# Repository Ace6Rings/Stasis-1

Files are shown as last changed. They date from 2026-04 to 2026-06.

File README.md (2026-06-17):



# OVERVIEW

The Reshular Robot Arm is a 6 DOF robotic arm. It is operated over bluetooth so it can be operated remotely.
5 stepper motors, using the TMC2209 driver, and 1 servo motor is used to make this huge robotic arm.

# Purpose

I made this because I've always been fascinated on how to use technology to make an impact on the physical world. 
I've seen small robotic arms powered with servo motors. But I noticed that scaling it up in size changes the materials I need 
and introduces (newish) problems like insufficient torque when using a servo motor. These robotic arms are also shorter ranged and can only hold
very light and small items. Thats why I built this robotic arm. I can lift items that are impossible for small robotic arms like a big book. 
The most important thing is that I became way better at eda since this is my first project that uses a smd PCB.

# Schematic
schematic 2
scematic1
There are 5 tmc 2209 motor drivers. They are almost identical. Only their gpio assignments to dir and step changes and also their uart configuration.

So how did I configure it and how can you too?

The tmc2209 talks to the esp32 via UART. But four tmc 2209s share one uart line. Wait, there's 5 tmcs, not 4! How could that be?
Well, the ID for uart is dictated by the whether your ms1 and ms2 are pulled high or low. Since there are 2 states and 2 pins, 2^2 is 4. So you get 4 combinations.
To account for the 5th tmc 2209, I just used another set of gpios.

The ms1 and ms2 pins also happen to control microstepping, and thats pretty important if you have something like an EV or a robot arm like this. So I put the finer microstepping onto parts that actually matter, such as the elbow joint. You can find further details via the datasheet for the TMC2209 and the exact configuration in the PCB file that I have.
# PCB
pcb

Now lets get into the PCB.
The specs of the PCB isn't anything special. It is a 2 layer pcb, and thats exactly why this is good. It's theoretically not gonna perform as well as a four layer board (well not really because this is a 2 layer board thing). But since its only 2 layers, the cost decreases significantly. There are two layers of electrical protection. The first one is the NCP1117 (well not really? but if it dies the circuit becomes open so I guess it is protection), and the second one is the TVS diode. The TVS diode is a component that protects your circuit when the voltage/current reaches a certain threshold. For something like a robot arm, you will defininately one that.
# Model
The purpose of the model is not to make it look good but to make it as light as possible to test in real life. 
It features 6 degrees of freedom, which could move (almost) ny item in any way you could think of.
model2
model1
The base has an hexagonal pattern which maximizes strength, aesthetics, and filament efficiency.
# Motor joints

Well, how does each joint work? Its actually quite simple. You can tell by the picture that the stepper motors are directly attached to each joint, so no special pullys or anything! This saves complexity and cost. For the gripper, its a little different.

The central gear meshes with the two side parts. When it spins, the two grippers come together and, well, grips. Spinning it the opposite way retracts it. You can try it out in this link.
https://cad.onshape.com/documents/dfb7d85a38278a669fcebbb5/w/2d92252d034fc83197e6695c/e/ec9dc79179103d4b89a939a4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



As you can see, the motor is directly attached.

# Testing

N/A (will include after getting parts)

# Bill of Materials

| Name | Purpose | Quantity | Total Cost (USD) | Link | Distributor |
|---|---|---|---|---|---|
| li ion batteries | batteries to power my robot arm | 1 | 25.98 | https://www.amazon.com/Mupoer-Rechargeable-Batteries-Integrated-Charging/dp/B0D4M581B3/ref=sr_1_15?sr=8-15 | amazon |
| ds3225 | gripper motor | 1 | 16.99 | https://www.amazon.com/gp/product/B0CNTG877G/ref=ox_sc_act_title_1?smid=A1PKC2PUMNR8VD | amazon |
| HEAT SET INSERTS | To assemble my robot arm | 1 | 9.98 | https://www.amazon.com/M2-M2-5-M3-Threaded-Inserts/dp/B0FH4JQ3VB/ref=sr_1_4?sr=8-4 | amazon |
| 175-TMC2209-LA-TCT-ND | IC MTR DRV 4.75-28V QFN28 | 10 | 40.89 | https://www.digikey.com/en/products/detail/analog-devices-inc-maxim-integrated/TMC2209-LA-T/10232491 | DIGIKEY |
| NCP1117LPST33T3GOSCT-ND | IC REG LINEAR 3.3V 1A SOT-223 | 10 | 2.62 | https://www.digikey.com/en/products/detail/onsemi/NCP1117LPST33T3G/1967376 | DIGIKEY |
| 296-50511-1-ND | UNIDIR PRECISION SURGE DIODE | 10 | 7.06 | https://www.digikey.com/en/products/detail/texas-instruments/TVS1400DRVR/11589096 | DIGIKEY |
| 2073-USB4085-GF-ACT-ND | CONN RCPT USB2.0 TYPE C 16+8POS | 2 | 2.15 | https://www.digikey.com/en/products/detail/gct/USB4085-GF-A/9859704 | DIGIKEY |
| CKN10285CT-ND | SWITCH TACTILE SPST-NO 0.05A 32V | 10 | 5.81 | https://www.digikey.com/en/products/detail/c-k/KMR241NG-ULC-LFS/2747141 | DIGIKEY |
| 490-10700-1-ND | CAP CER 0.1UF 50V X7R 0402 | 50 | 0.81 | https://www.digikey.com/en/products/detail/murata-electronics/GRM155R71H104KE14D/4358653 | DIGIKEY |
| 277-1722-ND | TERM BLK 3POS SIDE ENT 3.5MM PCB | 1 | 2.10 | https://www.digikey.com/en/products/detail/phoenix-contact/1984620/950937 | DIGIKEY |
| 1276-1096-1-ND | CAP CER 10UF 16V X5R 0805 | 10 | 0.54 | https://www.digikey.com/en/products/detail/samsung-electro-mechanics/CL21A106KOQNNNE/3886902 | DIGIKEY |
| 273-KDV12DR100ETCT-ND | RES 0.1 OHM 0.5% 1/2W 1206 | 25 | 3.00 | https://www.digikey.com/en/products/detail/ohmite/KDV12DR100ET/13691867 | DIGIKEY |
| 311-5.10KLRCT-ND | RES 5.1K OHM 1% 1/16W 0402 | 25 | 0.37 | https://www.digikey.com/en/products/detail/yageo/RC0402FR-075K1L/726633 | DIGIKEY |
| 541-10.0KLCT-ND | RES 10K OHM 1% 1/16W 0402 | 25 | 0.59 | https://www.digikey.com/en/products/detail/vishay-dale/CRCW040210K0FKED/1176095 | DIGIKEY |
| 311-100KLRCT-ND | RES 100K OHM 1% 1/16W 0402 | 25 | 0.37 | https://www.digikey.com/en/products/detail/yageo/RC0402FR-07100KL/726651 | DIGIKEY |
| 311-1.00KLRCT-ND | RES 1K OHM 1% 1/16W 0402 | 25 | 0.37 | https://www.digikey.com/en/products/detail/yageo/RC0402FR-071KL/726544 | DIGIKEY |
| 277-1721-ND | TERM BLK 2POS SIDE ENT 3.5MM PCB | 1 | 1.46 | https://www.digikey.com/en/products/detail/phoenix-contact/1984617/950934 | DIGIKEY |
| 490-4763-1-ND | CAP CER 0.022UF 50V X7R 0402 | 50 | 1.01 | https://www.digikey.com/en/products/detail/murata-electronics/GCM155R71H223KA55D/2756835 | DIGIKEY |
| 277-1860-ND | TERM BLK 4POS SIDE ENT 3.5MM PCB | 5 | 13.45 | https://www.digikey.com/en/products/detail/phoenix-contact/1984633/950950 | DIGIKEY |
| 1965-ESP32-S3-WROOM-1-N4CT-ND | RF TXRX MODULE BT PCB TRACE SMD | 2 | 11.46 | https://www.digikey.com/en/products/detail/espressif-systems/ESP32-S3-WROOM-1-N4/16162639 | DIGIKEY |
| JLCPCB | To put my components on | 1 | 36.48 | https://trade.jlcpcb.com/checkout/payMethod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 | jlcpcb |
| NEMA 17 motor thin | For the arms | 5 | 17.50 | https://www.alibaba.com/product-detail/Special-Offer-26mm-Length-NEMA-17_1601043669710.html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 | Alibaba |
| M2-M5 assortment screws | To screw pcb, battery holders, and | 1 | 12.38 | https://www.amazon.com/Countersunk-Assortment-Phillips-Machine-Washers/dp/B0F87JTJ6T/ref=sr_1_3?sr=8-3 | Amazon |
| mr105 | bearings for high torque load | 4 | 8.79 | https://www.amazon.com/MR105-2RS-Deep-Groove-Ball-Bearings/dp/B0DXZNSMJC/ref=sr_1_6?sr=8-6 | amazon |

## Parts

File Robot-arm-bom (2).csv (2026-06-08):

Name | Purpose | Quantity | Total Cost (USD) | Link | Distributor
Helping hands | I need it to solder my pcb | 1 | 16.99 | https://www.amazon.com/XYK-Helping-Soldering-Flexible-Electronic/dp/B0BHHVP467/ref=sr_1_10?sr=8-10 | Amazon
Heat gun soldering station | To solder my pcb | 1 | 35.49 | https://www.amazon.com/Soldering-Station-Electric-Temperature-Functions/dp/B0DP73JYDB | Amazon
Hot Plate | To solder my pcb | 1 | 29.99 | https://www.amazon.com/Soldering-Microcomputer-Technicians-Electronics-Enthusiasts/dp/B0G443BG4X | Amazon
tmc2209-la-t | To drive my motor | 5 | 16.22 | https://www.aliexpress.us/item/3256810347096939.html?curPageLogUid=BgZfQMcNk5lT | aliexpress
CAP CER 0.1UF 50V X7R 0402 |  | 50 | 0.81 | https://www.digikey.com/en/products/result?keywords=490-10700-1-ND
CAP CER 0.022UF 50V X7R 0402 |  | 50 | 1.01 | https://www.digikey.com/en/products/result?keywords=490-4763-1-ND
CAP CER 10UF 16V X5R 0805 |  | 10 | 0.54 | https://www.digikey.com/en/products/result?keywords=1276-1096-1-ND
TERM BLK 2POS SIDE ENT 3.5MM PCB |  | 1 | 1.46 | https://www.digikey.com/en/products/result?keywords=277-1721-ND
TERM BLK 3POS SIDE ENT 3.5MM PCB |  | 1 | 2.10 | https://www.digikey.com/en/products/result?keywords=277-1722-ND
TERM BLK 4POS SIDE ENT 3.5MM PCB |  | 5 | 13.45 | https://www.digikey.com/en/products/result?keywords=277-1860-ND
RES 0.1 OHM 0.5% 1/2W 1206 |  | 25 | 3.00 | https://www.digikey.com/en/products/result?keywords=273-KDV12DR100ETCT-ND
RES 5.1K OHM 1% 1/16W 0402 |  | 25 | 0.37 | https://www.digikey.com/en/products/result?keywords=311-5.10KLRCT-ND
RES 10K OHM 1% 1/16W 0402 |  | 25 | 0.59 | https://www.digikey.com/en/products/result?keywords=541-10.0KLCT-ND
RES 100K OHM 1% 1/16W 0402 |  | 25 | 0.37 | https://www.digikey.com/en/products/result?keywords=311-100KLRCT-ND
RES 1K OHM 1% 1/16W 0402 |  | 25 | 0.37 | https://www.digikey.com/en/products/result?keywords=311-1.00KLRCT-ND
IC REG LINEAR 3.3V 1A SOT-223 |  | 10 | 2.62 | https://www.digikey.com/en/products/result?keywords=NCP1117LPST33T3GOSCT-ND
UNIDIR PRECISION SURGE DIODE |  | 2 | 2.06 | https://www.digikey.com/en/products/result?keywords=296-50511-1-ND | Digikey
CONN RCPT USB2.0 TYPE C 16+8POS |  | 2 | 2.15 | https://www.digikey.com/en/products/result?keywords=2073-USB4085-GF-ACT-ND
SWITCH TACTILE SPST-NO 0.05A 32V |  | 10 | 5.81 | https://www.digikey.com/en/products/result?keywords=CKN10285CT-ND
RF TXRX MODULE BT PCB TRACE SMD |  | 1 | 5.21 | https://www.digikey.com/en/products/result?keywords=1965-ESP32-S3-WROOM-1-N4CT-ND | digikey
3mmx75mm rod | for my gripper | 1 | 9.19 | https://www.amazon.com/gp/product/B08M3VXR6W/ref=ox_sc_act_title_1?smid=A1THAZDOWP300U | amazon
steel rods | for my gearbox | 25 | 4.44 | https://www.amazon.com/TOP-VIGOR-Support-Stainless-Cylindrical-Elements/dp/B0D5CHMG2C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 | amazon
bushings | for my gear box | 10 | 1.75 | https://www.aliexpress.us/item/3256803849223368.html?mp=1 | aliexpress
6805 bearings | for my gearbox | 4 | 3.52 | https://www.aliexpress.us/item/3256806312258090.html?mp=1 | aliexpress
li ion batteries | batteries to power my robot arm | 1 | 9.51 | https://www.aliexpress.us/item/3256810317114752.html?curPageLogUid=wJq9dV0At72m | aliexpress
ds3225 | gripper motor | 1 | 16.99 | https://www.amazon.com/gp/product/B0CNTG877G/ref=ox_sc_act_title_1?smid=A1PKC2PUMNR8VD | amazon
HEAT SET INSERTS | To assemble my robot arm | 1 | 9.98 | https://www.amazon.com/M2-M2-5-M3-Threaded-Inserts/dp/B0FH4JQ3VB/ref=sr_1_4?sr=8-4 | amazon
JLCPCB | To put my components on | 1 | 9.11 | https://trade.jlcpcb.com/checkout/payMethod?systemType=order_pcb&calType=PAY&batchNum=W2026042809527003 | jlcpcb
NEMA 17 motor thin | For the arms | 5 | 17.50 | https://www.alibaba.com/product-detail/Special-Offer-26mm-Length-NEMA-17_1601043669710.html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 | Alibaba
M2-M5 assortment screws | To screw pcb, battery holders, and | 1 | 12.38 | https://www.amazon.com/Countersunk-Assortment-Phillips-Machine-Washers/dp/B0F87JTJ6T | Amazon
mr105 | bearings for high torque load | 1 | 8.79 | https://www.amazon.com/MR105-2RS-Deep-Groove-Ball-Bearings/dp/B0DXZNSMJC/ref=sr_1_6?sr=8-6 | amazon
$294.78

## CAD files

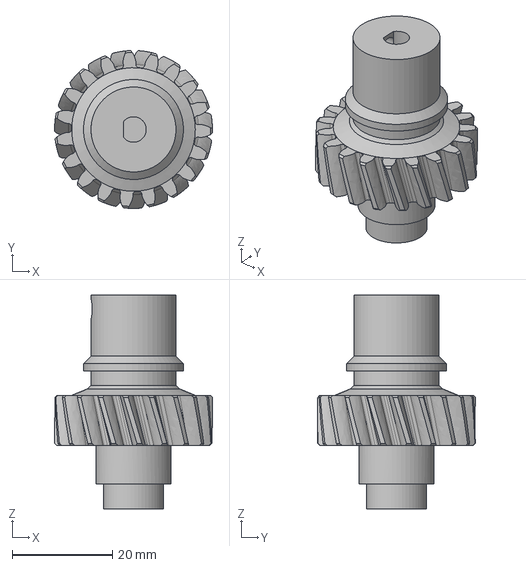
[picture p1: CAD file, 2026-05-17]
Stasis-Robotic-Arm/3D printer files/Base turn - Input shaft.step
31.5 x 31.5 x 42.7 mm

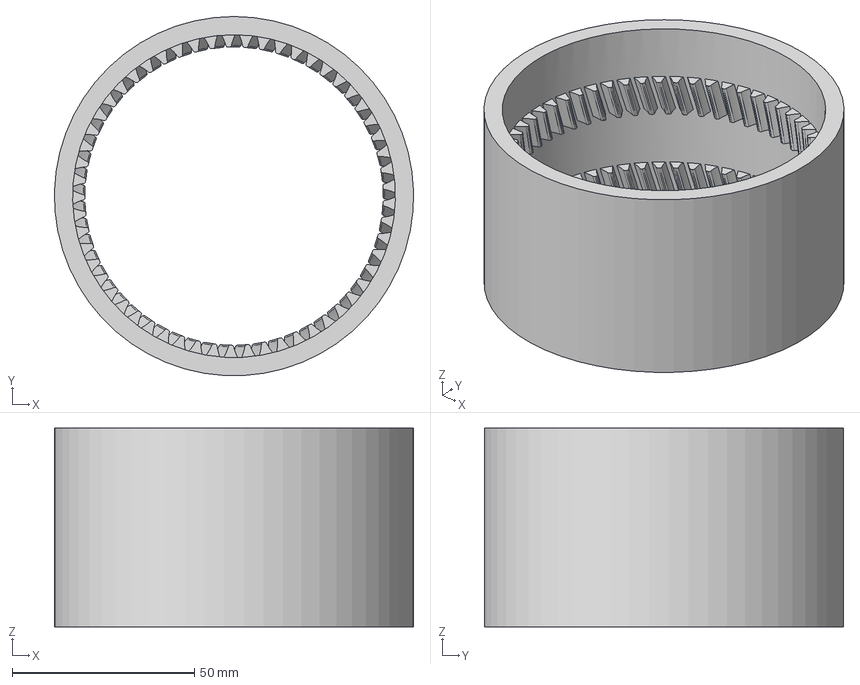
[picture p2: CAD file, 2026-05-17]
Stasis-Robotic-Arm/3D printer files/Base turn - ring gear.step
98.5 x 98.4 x 54.5 mm

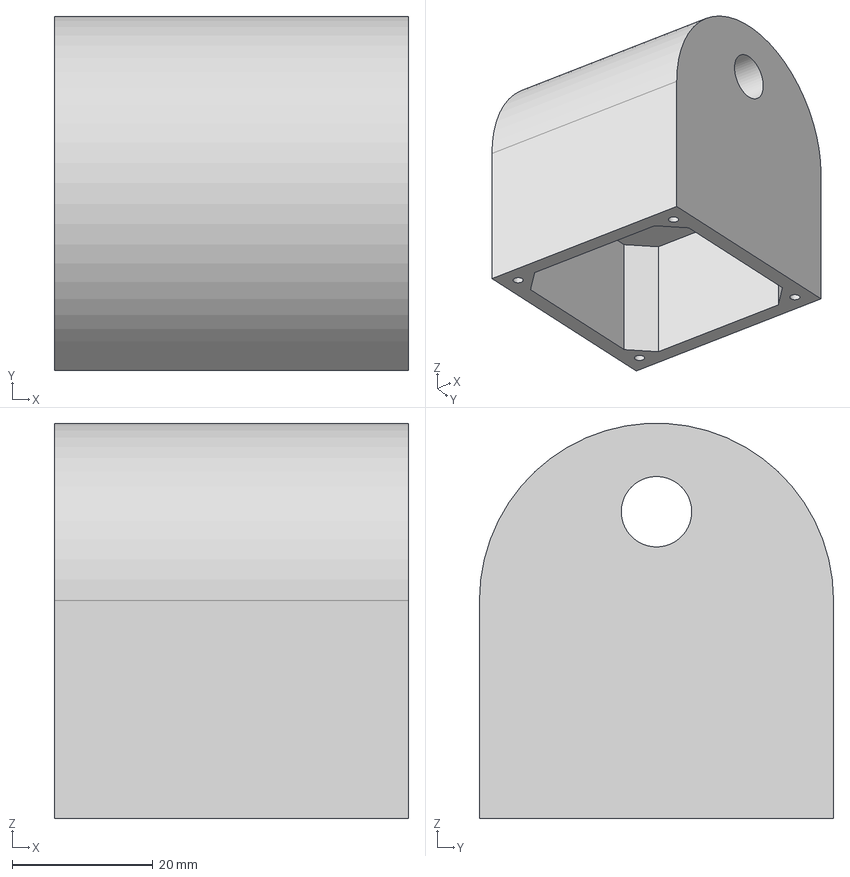
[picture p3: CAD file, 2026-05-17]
Stasis-Robotic-Arm/3D printer files/Base turn - Part 2.step
50.3 x 50.3 x 56.1 mm

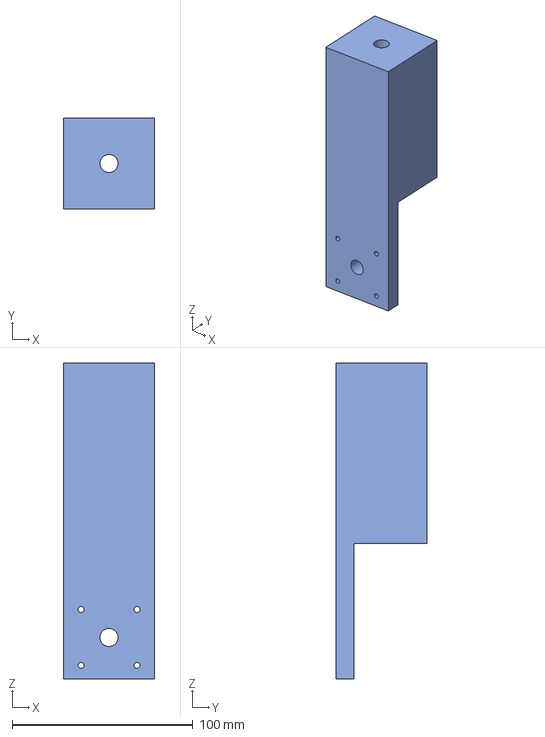
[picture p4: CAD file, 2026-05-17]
Stasis-Robotic-Arm/3D printer files/Base turn - Part 3.step
50.3 x 50.3 x 175.0 mm

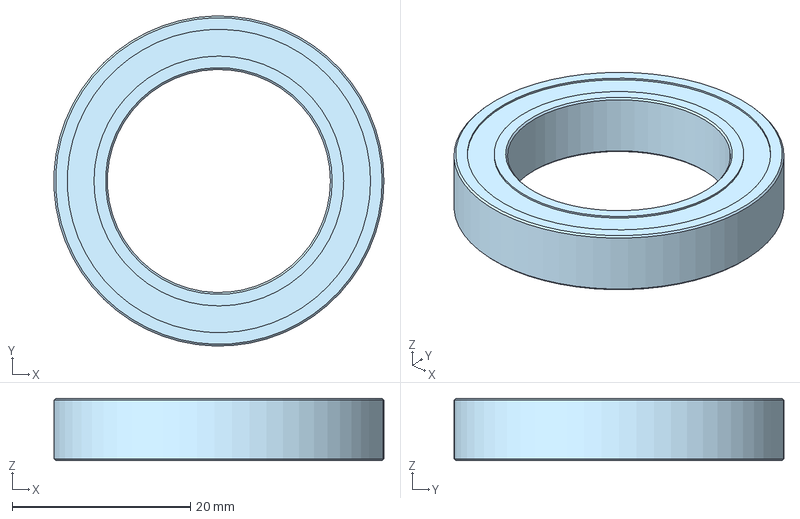
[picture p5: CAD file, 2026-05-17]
Stasis-Robotic-Arm/3D printer files/Base turn - Bearing 25x37x7mm.step
37.0 x 37.0 x 7.00 mm

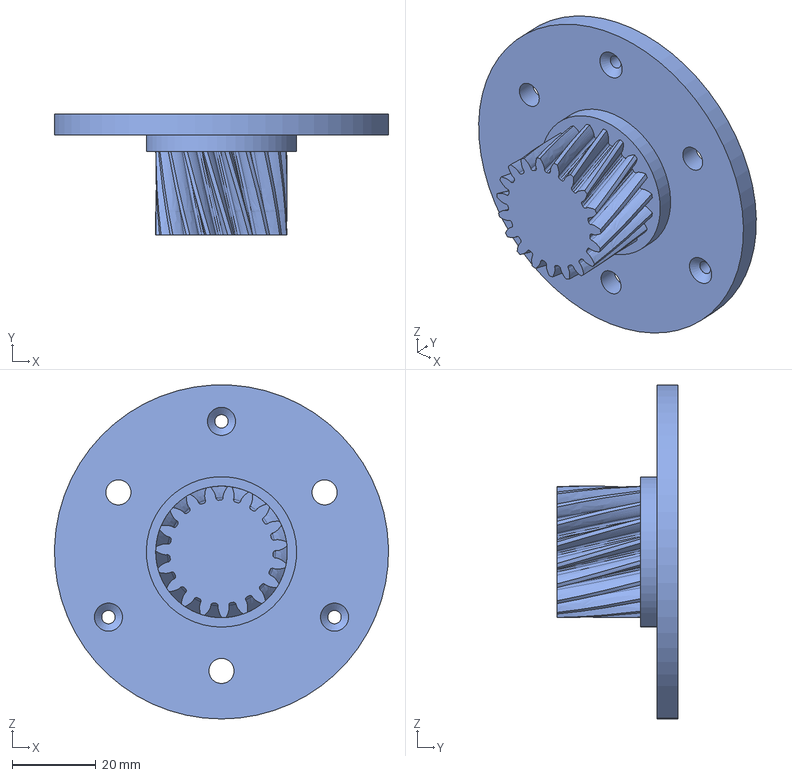
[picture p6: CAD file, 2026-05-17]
Stasis-Robotic-Arm/3D printer files/Base turn - Spur gear (19 teeth).step
80.0 x 29.0 x 79.9 mm

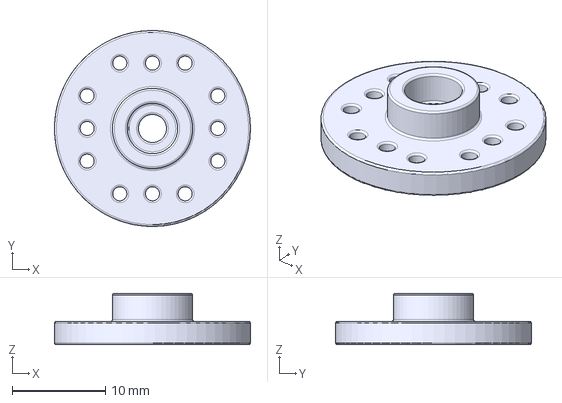
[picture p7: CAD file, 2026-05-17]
Stasis-Robotic-Arm/3D printer files/Base turn - Circular Servo Horn.step
21.0 x 21.0 x 5.50 mm

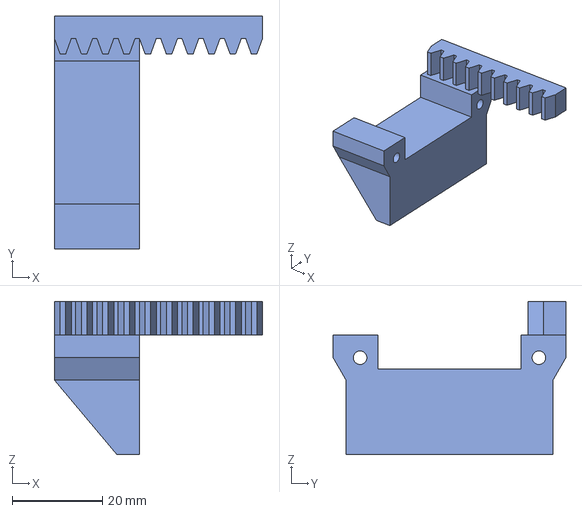
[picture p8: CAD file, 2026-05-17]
Stasis-Robotic-Arm/3D printer files/Base turn - Part 9.step
46.1 x 51.6 x 34.0 mm

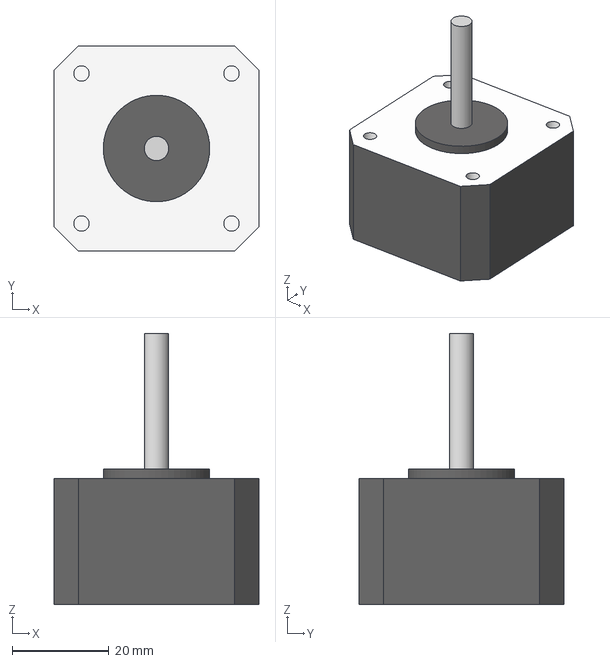
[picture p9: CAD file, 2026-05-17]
Stasis-Robotic-Arm/3D printer files/Base turn - Part 1 (10).step
42.3 x 42.3 x 56.0 mm

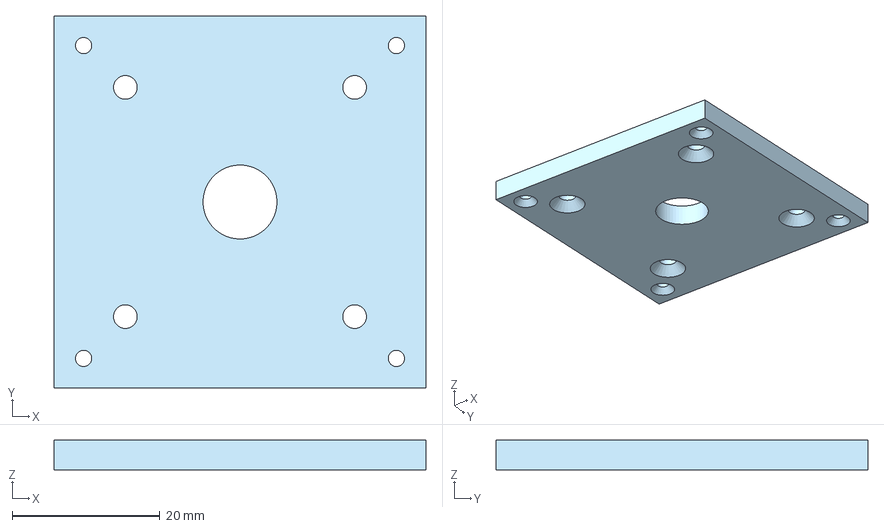
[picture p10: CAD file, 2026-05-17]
Stasis-Robotic-Arm/3D printer files/Base turn - Part 1.step
50.3 x 50.3 x 4.00 mm

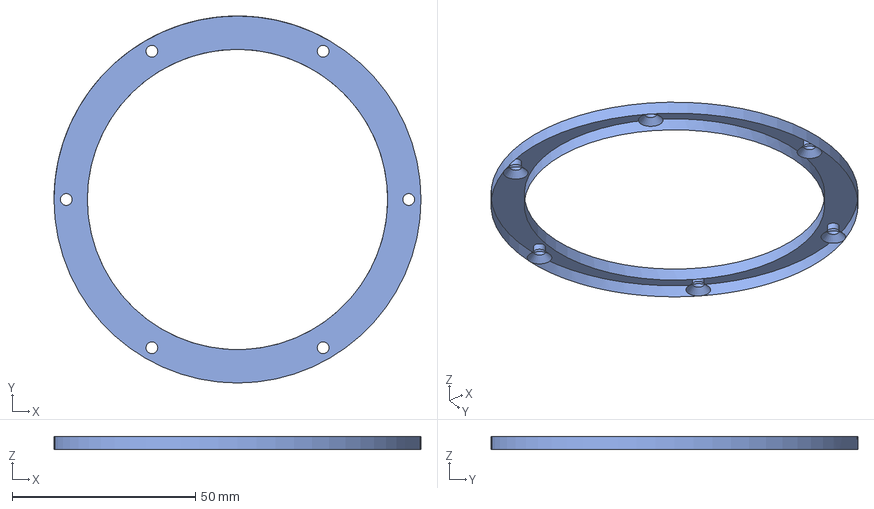
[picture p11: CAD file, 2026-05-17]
Stasis-Robotic-Arm/3D printer files/Base turn - Part 4.step
100.2 x 100.2 x 3.48 mm

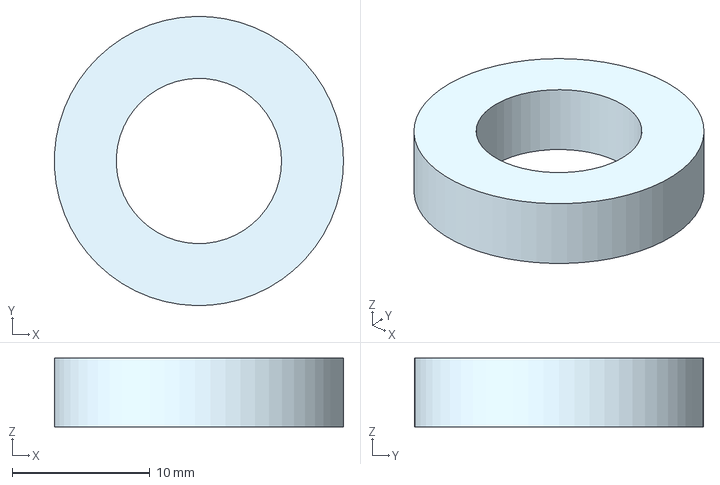
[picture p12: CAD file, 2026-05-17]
Stasis-Robotic-Arm/3D printer files/Base turn - Part 6.step
21.0 x 21.0 x 5.00 mm

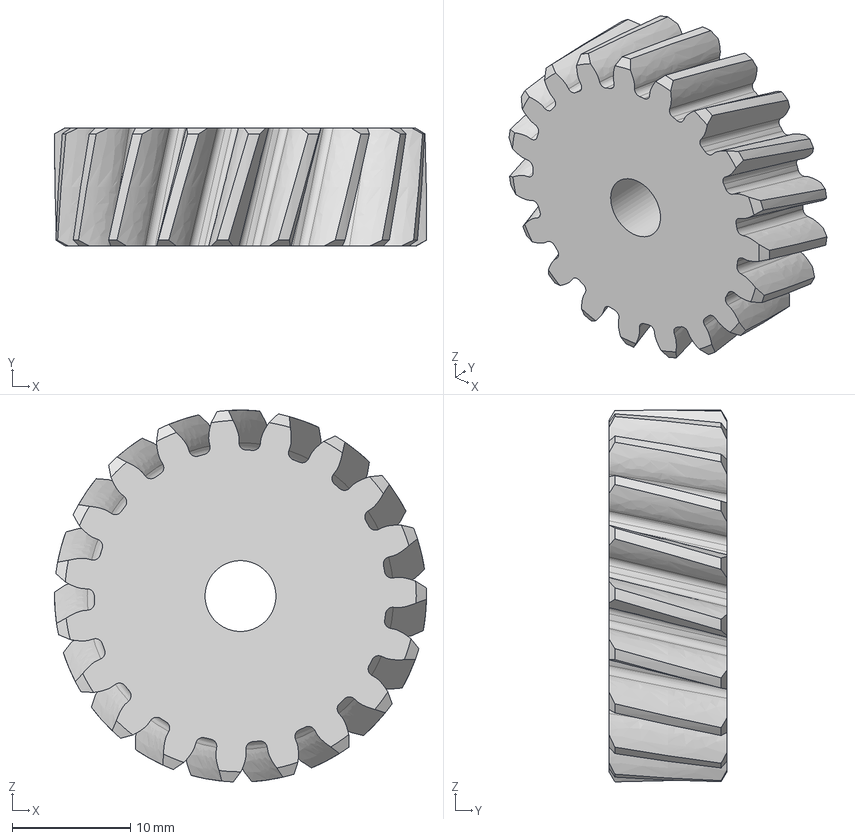
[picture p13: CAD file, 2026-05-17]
Stasis-Robotic-Arm/3D printer files/Base turn - planet gear.step
31.5 x 10.0 x 31.5 mm

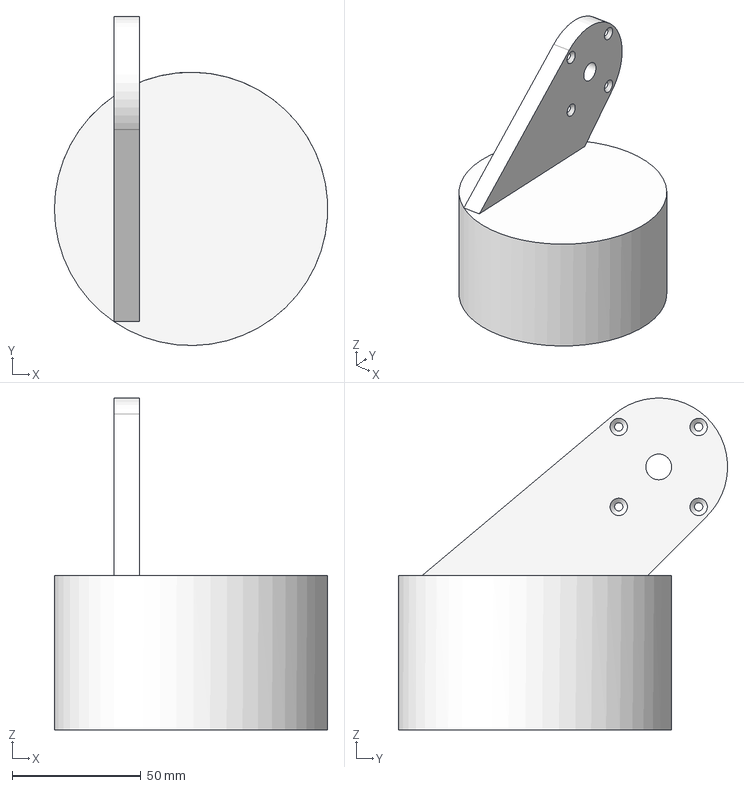
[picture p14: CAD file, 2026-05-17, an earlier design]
Stasis-Robotic-Arm/3D printer files/Base turn - Part 2 (3).step
105.9 x 127.6 x 128.7 mm

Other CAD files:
Stasis-Robotic-Arm/3D printer files/bambu_sliced.gcode.3mf
Stasis-Robotic-Arm/3D printer files/Base turn - Part 1 (11).step
Stasis-Robotic-Arm/3D printer files/Base turn - Part 9 (1).step
Stasis-Robotic-Arm/3D printer files/Base turn - Part 1 (5).step
Stasis-Robotic-Arm/3D printer files/Base turn - Part 1 (1).step
Stasis-Robotic-Arm/3D printer files/Base turn - Part 1 (2).step
Stasis-Robotic-Arm/3D printer files/Base turn - Part 1 (3).step
Stasis-Robotic-Arm/3D printer files/Base turn - Part 1 (4).step
Stasis-Robotic-Arm/3D printer files/Base turn - Part 1 (6).step
Stasis-Robotic-Arm/3D printer files/Base turn - Part 1 (7).step
Stasis-Robotic-Arm/3D printer files/Base turn - Part 1 (8).step
Stasis-Robotic-Arm/3D printer files/Base turn - Part 1 (9).step
Stasis-Robotic-Arm/3D printer files/Base turn - Part 2 (1).step
Stasis-Robotic-Arm/3D printer files/Base turn - Part 2 (2).step
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

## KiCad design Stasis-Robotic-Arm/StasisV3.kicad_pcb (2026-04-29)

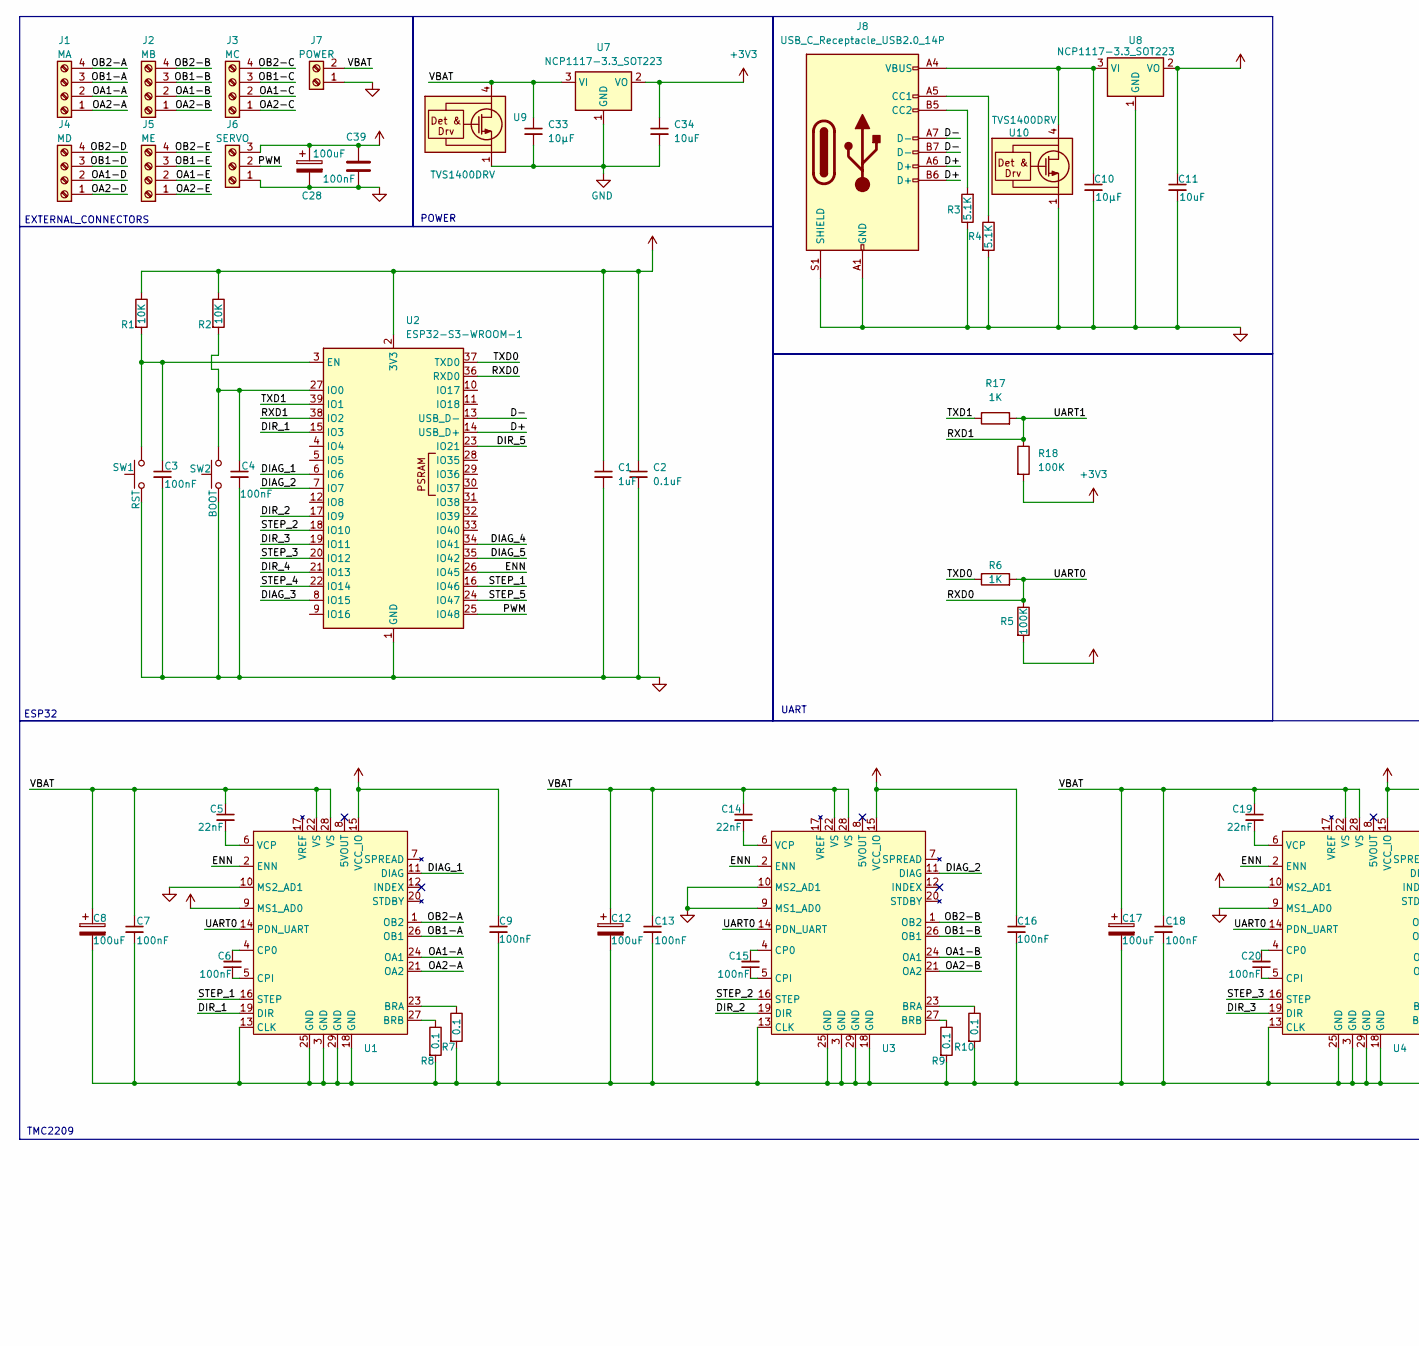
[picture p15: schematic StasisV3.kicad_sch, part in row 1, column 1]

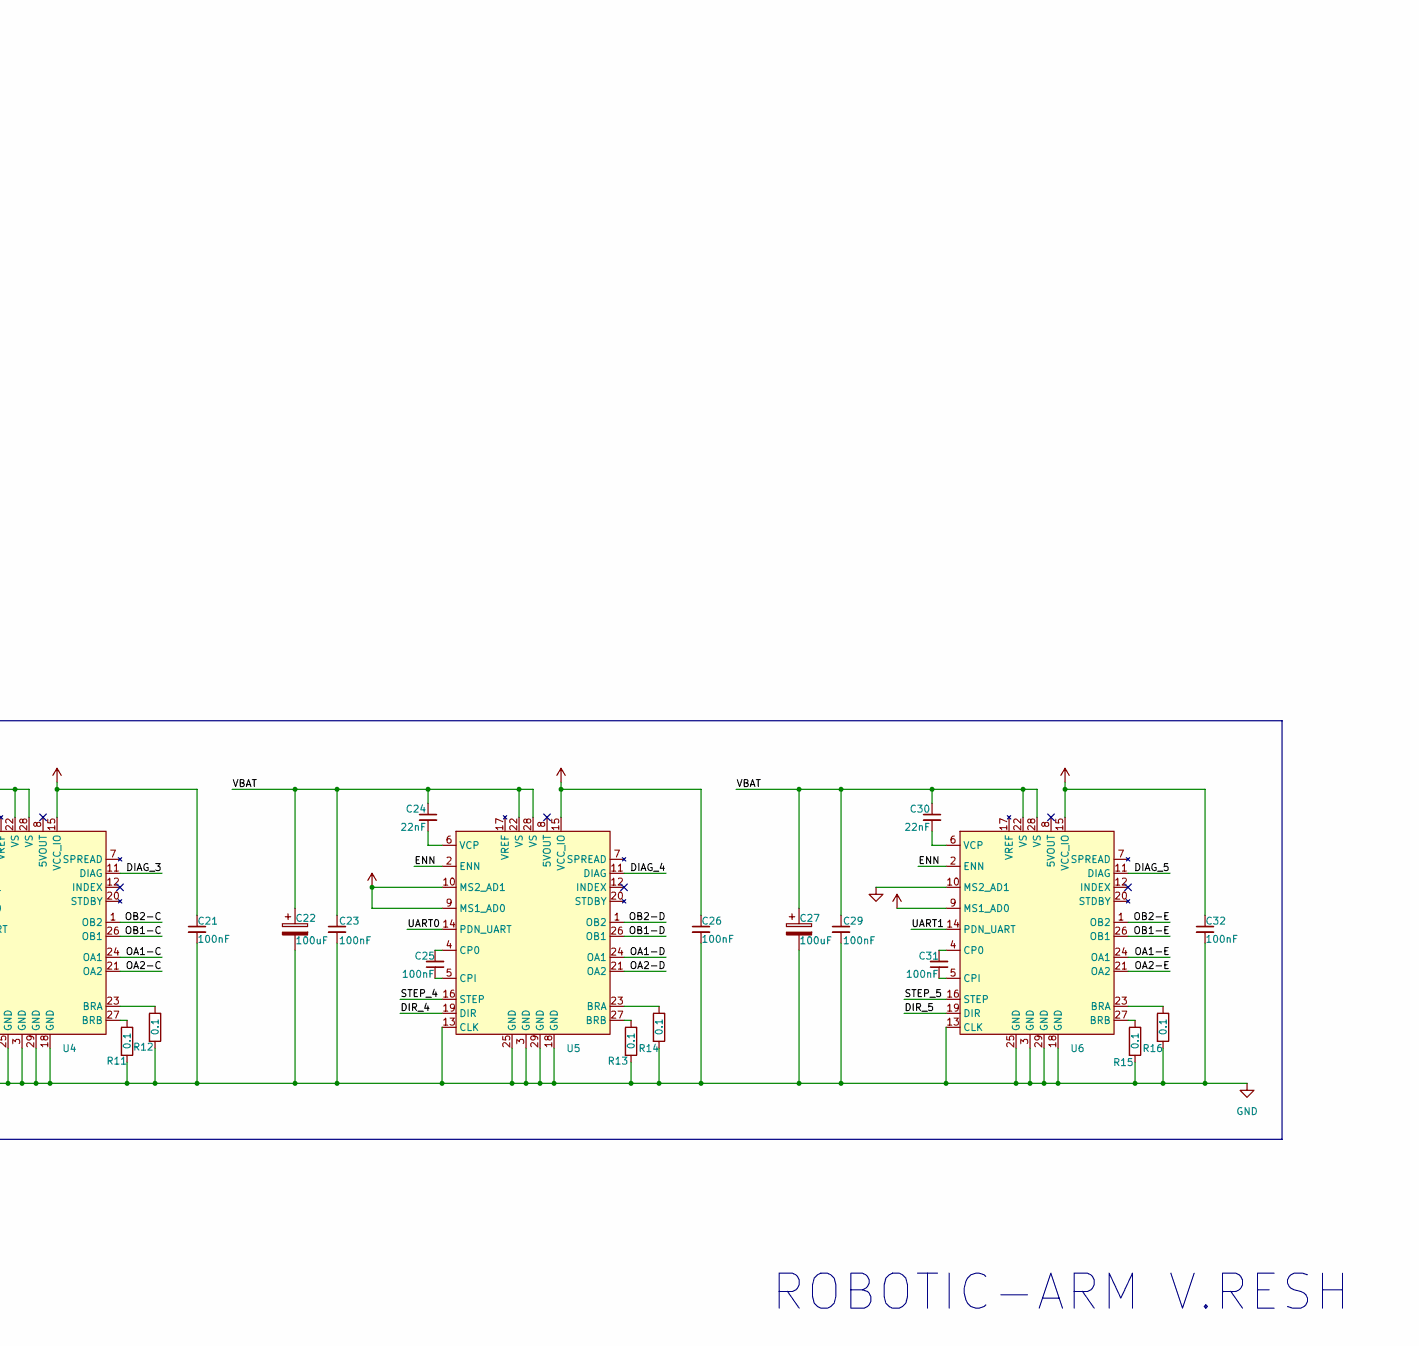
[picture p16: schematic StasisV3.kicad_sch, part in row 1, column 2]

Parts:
C1: 1uF; C_0402_1005Metric
C2: 0.1uF; C_0402_1005Metric
C3, C4, C6, C7, C9, C13, C15, C16, C18, C20, C21, C23, C25, C26, C29, C31, C32, C39: 100nF; C_0402_1005Metric
C5, C14, C19, C24, C30: 22nF; C_0402_1005Metric
C8, C12, C17, C22, C27, C28: 100uF; CP_EIA-6032-28_Kemet-C
C10, C33: 10μF; C_0805_2012Metric
C11, C34: 10uF; C_0805_2012Metric
J1: MA; TerminalBlock_Phoenix_PT-1,5-4-3.5-H_1x04_P3.50mm_Horizontal
J2: MB; TerminalBlock_Phoenix_PT-1,5-4-3.5-H_1x04_P3.50mm_Horizontal
J3: MC; TerminalBlock_Phoenix_PT-1,5-4-3.5-H_1x04_P3.50mm_Horizontal
J4: MD; TerminalBlock_Phoenix_PT-1,5-4-3.5-H_1x04_P3.50mm_Horizontal
J5: ME; TerminalBlock_Phoenix_PT-1,5-4-3.5-H_1x04_P3.50mm_Horizontal
J6: SERVO; TerminalBlock_Phoenix_PT-1,5-3-3.5-H_1x03_P3.50mm_Horizontal
J7: POWER; TerminalBlock_Phoenix_PT-1,5-2-3.5-H_1x02_P3.50mm_Horizontal
J8: USB_C_Receptacle_USB2.0_14P; USB_C_Receptacle_GCT_USB4105-xx-A_16P_TopMnt_Horizontal
R1, R2: 10K; R_0402_1005Metric
R3, R4: 5.1K; R_0402_1005Metric
R5, R18: 100K; R_0402_1005Metric
R6, R17: 1K; R_0402_1005Metric
R7, R8, R9, R10, R11, R12, R13, R14, R15, R16: 0.1; R_1206_3216Metric
SW1: RST; SW_Push_1P1T_NO_CK_KMR2
SW2: BOOT; SW_Push_1P1T_NO_CK_KMR2
U1, U3, U4, U5, U6: tmc2209
U2: ESP32-S3-WROOM-1
U7, U8: NCP1117-3.3_SOT223; SOT-223-3_TabPin2
U9, U10: TVS1400DRV; WSON-6-1EP_2x2mm_P0.65mm_EP1x1.6mm

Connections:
+3V3: C1.1, C2.1, C9.1, C11.1, C16.1, C21.1, C26.1, C32.1, C34.1, R1.1, R2.1, R5.2, R18.2, U1.9 (MS1_AD0), U1.15 (VCC_IO), U2.2 (3V3), U3.15 (VCC_IO), U4.10 (MS2_AD1), U4.15 (VCC_IO), U5.9 (MS1_AD0), U5.10 (MS2_AD1), U5.15 (VCC_IO), U6.9 (MS1_AD0), U6.15 (VCC_IO), U7.2 (VO), U8.2 (VO)
/D+: J8.A6 (D+), J8.B6 (D+), U2.14 (USB_D+)
/D-: J8.A7 (D-), J8.B7 (D-), U2.13 (USB_D-)
/DIAG_1: U1.11 (DIAG), U2.6 (IO6)
/DIAG_2: U2.7 (IO7), U3.11 (DIAG)
/DIAG_3: U2.8 (IO15), U4.11 (DIAG)
/DIAG_4: U2.34 (IO41), U5.11 (DIAG)
/DIAG_5: U2.35 (IO42), U6.11 (DIAG)
/DIR_1: U1.19 (DIR), U2.15 (IO3)
/DIR_2: U2.17 (IO9), U3.19 (DIR)
/DIR_3: U2.19 (IO11), U4.19 (DIR)
/DIR_4: U2.21 (IO13), U5.19 (DIR)
/DIR_5: U2.23 (IO21), U6.19 (DIR)
/ENN: U1.2 (ENN), U2.26 (IO45), U3.2 (ENN), U4.2 (ENN), U5.2 (ENN), U6.2 (ENN)
/OA1-A: J1.2, U1.24 (OA1)
/OA1-B: J2.2, U3.24 (OA1)
/OA1-C: J3.2, U4.24 (OA1)
/OA1-D: J4.2, U5.24 (OA1)
/OA1-E: J5.2, U6.24 (OA1)
/OA2-A: J1.1, U1.21 (OA2)
/OA2-B: J2.1, U3.21 (OA2)
/OA2-C: J3.1, U4.21 (OA2)
/OA2-D: J4.1, U5.21 (OA2)
/OA2-E: J5.1, U6.21 (OA2)
/OB1-A: J1.3, U1.26 (OB1)
/OB1-B: J2.3, U3.26 (OB1)
/OB1-C: J3.3, U4.26 (OB1)
/OB1-D: J4.3, U5.26 (OB1)
/OB1-E: J5.3, U6.26 (OB1)
/OB2-A: J1.4, U1.1 (OB2)
/OB2-B: J2.4, U3.1 (OB2)
/OB2-C: J3.4, U4.1 (OB2)
/OB2-D: J4.4, U5.1 (OB2)
/OB2-E: J5.4, U6.1 (OB2)
/PWM: J6.2, U2.25 (IO48)
/RXD0: R5.1, R6.2, U1.14 (PDN_UART), U2.36 (RXD0), U3.14 (PDN_UART), U4.14 (PDN_UART), U5.14 (PDN_UART)
/RXD1: R17.2, R18.1, U2.38 (IO2), U6.14 (PDN_UART)
/STEP_1: U1.16 (STEP), U2.16 (IO46)
/STEP_2: U2.18 (IO10), U3.16 (STEP)
/STEP_3: U2.20 (IO12), U4.16 (STEP)
/STEP_4: U2.22 (IO14), U5.16 (STEP)
/STEP_5: U2.24 (IO47), U6.16 (STEP)
/TXD0: R6.1, U2.37 (TXD0)
/TXD1: R17.1, U2.39 (IO1)
unnamed: J8.A5 (CC1), R4.1
unnamed: J8.B5 (CC2), R3.2
unnamed: R7.1, U1.23 (BRA)
unnamed: R8.1, U1.27 (BRB)
unnamed: C6.2, U1.4 (CP0)
unnamed: C6.1, U1.5 (CPI)
unnamed: C5.2, U1.6 (VCP)
unnamed: R10.1, U3.23 (BRA)
unnamed: R9.1, U3.27 (BRB)
unnamed: C15.2, U3.4 (CP0)
unnamed: C15.1, U3.5 (CPI)
unnamed: C14.2, U3.6 (VCP)
unnamed: R12.1, U4.23 (BRA)
unnamed: R11.1, U4.27 (BRB)
unnamed: C20.2, U4.4 (CP0)
unnamed: C20.1, U4.5 (CPI)
unnamed: C19.2, U4.6 (VCP)
unnamed: R14.1, U5.23 (BRA)
unnamed: R13.1, U5.27 (BRB)
unnamed: C25.2, U5.4 (CP0)
unnamed: C25.1, U5.5 (CPI)
unnamed: C24.2, U5.6 (VCP)
unnamed: R16.1, U6.23 (BRA)
unnamed: R15.1, U6.27 (BRB)
unnamed: C31.2, U6.4 (CP0)
unnamed: C31.1, U6.5 (CPI)
unnamed: C30.2, U6.6 (VCP)
unnamed: C10.1, J8.A4 (VBUS), J8.A9 (VBUS), J8.B4 (VBUS), J8.B9 (VBUS), U8.3 (VI), U10.4 (IN), U10.5 (IN), U10.6 (IN)
VBAT: C5.1, C7.1, C8.1, C12.1, C13.1, C14.1, C17.1, C18.1, C19.1, C22.1, C23.1, C24.1, C27.1, C28.1, C29.1, C30.1, C33.1, C39.2, J6.3, J7.2, U1.22 (VS), U1.28 (VS), U3.22 (VS), U3.28 (VS), U4.22 (VS), U4.28 (VS), U5.22 (VS), U5.28 (VS), U6.22 (VS), U6.28 (VS), U7.3 (VI), U9.4 (IN), U9.5 (IN), U9.6 (IN)

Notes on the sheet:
TMC2209
POWER
UART
ESP32
EXTERNAL_CONNECTORS
ROBOTIC-ARM V.RESH

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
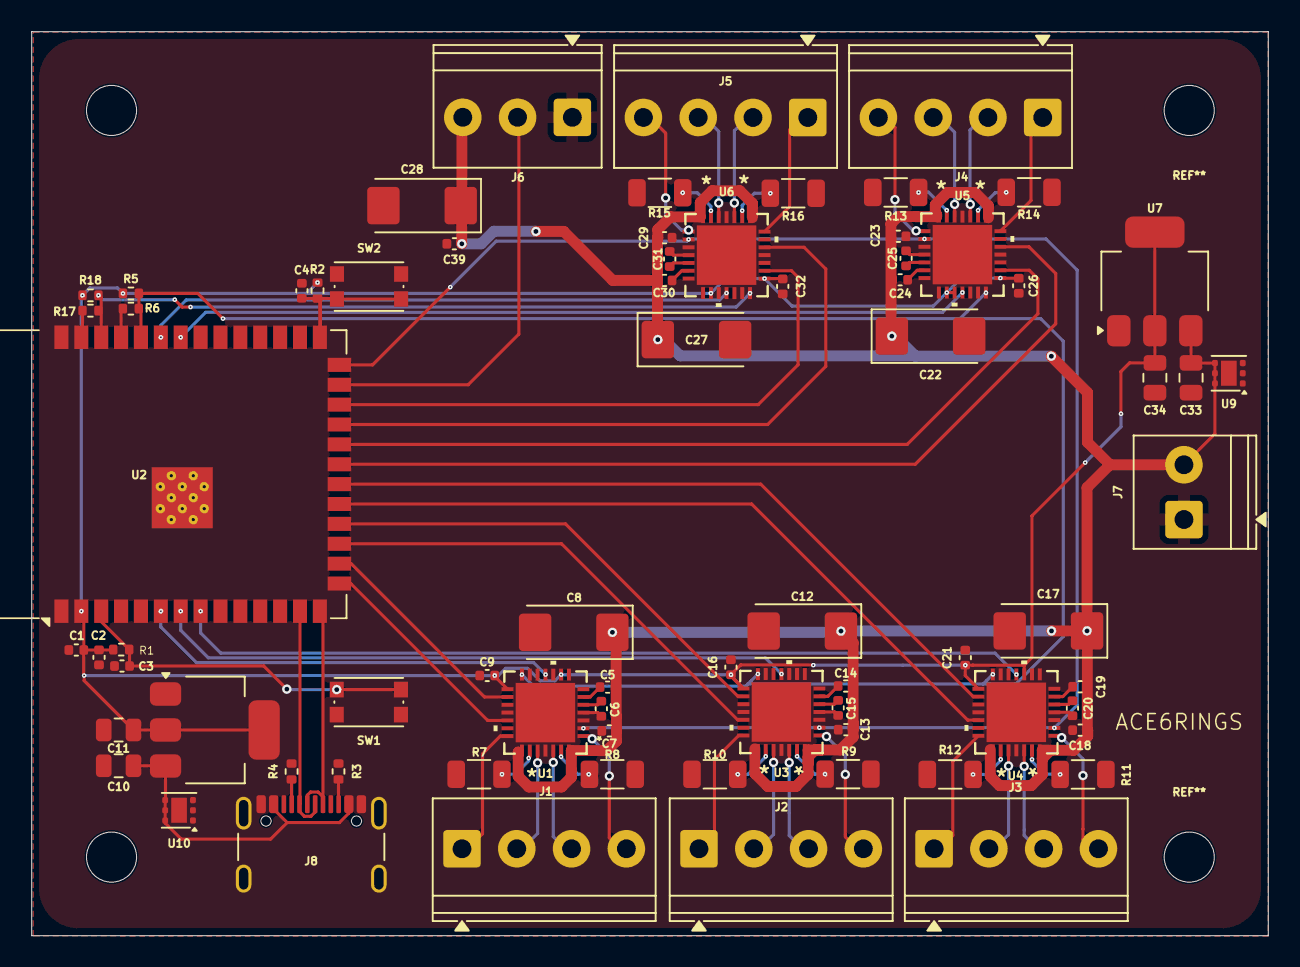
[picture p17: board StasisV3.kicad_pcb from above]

Board: 2 copper layers, 79.0 x 57.8 mm, 73 parts (0 on the bottom side), 76 nets.

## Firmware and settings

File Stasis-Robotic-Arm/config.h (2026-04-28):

#define MY_SSID       "YOUR_SSID"
#define MY_PASS       "YOUR_PASSWORD"
#ifndef CONFIG_H
#define CONFIG_H
#define OTA_HOSTNAME  "stasis-arm"
 
// Bus 1: GPIO1 (TX) / GPIO2 (RX) — drivers 1-4 (addresses 0-3)
// Bus 2: GPIO17 (TX) / GPIO18 (RX) — driver 5 (address 0)
#define TMC_BUS1_TX   1
#define TMC_BUS1_RX   2
#define TMC_BUS2_TX   17
#define TMC_BUS2_RX   18
#define TMC_BAUD      115200
#define R_SENSE       0.10f
 
#define STEP_1  5
#define DIR_1   4
#define STEP_2  6
#define DIR_2   7
#define STEP_3  9
#define DIR_3   10
#define STEP_4  11
#define DIR_4   12
#define STEP_5  13
#define DIR_5   8
 
#define DIAG_1  21
#define DIAG_2  38
#define DIAG_3  39
#define DIAG_4  44
#define DIAG_5  43
 
#define SERVO_PIN  47
 
#define DEFAULT_CURRENT_MA   800
#define DEFAULT_MICROSTEPS   16
#define DEFAULT_SPEED        400
#define DEFAULT_ACCEL        800
#define SERVO_MIN_US   500
#define SERVO_MAX_US   2500
 
#define SERIAL_BUF_SIZE  128
#define NUM_JOINTS       5
 
#endif

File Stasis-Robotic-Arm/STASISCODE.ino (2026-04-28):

#include <Arduino.h>
#include <WiFi.h>
#include <ArduinoOTA.h>
#include <ESP32Servo.h>
#include "config.h" 
#include "stepper_ctrl.h"
 
static Servo gripper;
static int   servoAngle = 90;
 
static char   cmdBuf[SERIAL_BUF_SIZE];
static size_t cmdIdx = 0;
 
static bool wifiConnected = false;
 
void wifi_init() {
    Serial.printf("[WIFI] Connecting to %s", MY_SSID);
    WiFi.mode(WIFI_STA);
    WiFi.setHostname(OTA_HOSTNAME);
    WiFi.begin(MY_SSID, MY_PASS);
 
    uint32_t start = millis();
    while (WiFi.status() != WL_CONNECTED && (millis() - start) < 10000) {
        delay(250);
        Serial.print(".");
    }
 
    if (WiFi.status() == WL_CONNECTED) {
        wifiConnected = true;
        Serial.printf("\n[WIFI] Connected: %s\n", WiFi.localIP().toString().c_str());
    } else {
        Serial.println("\n[WIFI] Not connected — OTA unavailable, USB only");
    }
}
 
void ota_init() {
    if (!wifiConnected) return;
 
    ArduinoOTA.setHostname(OTA_HOSTNAME);
 
    ArduinoOTA.onStart([]() {
        stepper_emergency_stop();
        Serial.println("[OTA] Update starting...");
    });
 
    ArduinoOTA.onEnd([]() {
        Serial.println("[OTA] Update complete. Rebooting...");
    });
 
    ArduinoOTA.onProgress([](unsigned int progress, unsigned int total) {
        Serial.printf("[OTA] %u%%\r", (progress * 100) / total);
    });
 
    ArduinoOTA.onError([](ota_error_t error) {
        Serial.printf("[OTA] Error %u: ", error);
        switch (error) {
            case OTA_AUTH_ERROR:    Serial.println("Auth failed");    break;
            case OTA_BEGIN_ERROR:   Serial.println("Begin failed");   break;
            case OTA_CONNECT_ERROR: Serial.println("Connect failed"); break;
            case OTA_RECEIVE_ERROR: Serial.println("Receive failed"); break;
            case OTA_END_ERROR:     Serial.println("End failed");     break;
        }
    });
 
    ArduinoOTA.begin();
    Serial.printf("[OTA] Ready at %s.local\n", OTA_HOSTNAME);
}
 
void print_help() {
    Serial.println("=== Stasis Robotic Arm ===");
    Serial.println("M <joint> <steps> <speed>  Move joint (neg steps=reverse)");
    Serial.println("H <joint>                  Home joint via StallGuard");
    Serial.println("S <angle>                  Set servo (0-180)");
    Serial.println("C <joint> <mA>             Set motor current");
    Serial.println("P                          Print all positions");
    Serial.println("E                          Emergency stop");
    Serial.println("R                          Re-enable motors");
    Serial.println("?                          This help");
}
 
void process_command(const char* cmd) {
    if (cmd[0] == '\0') return;
 
    char type = cmd[0];
    int joint, steps, currentMA, angle;
    float speed;
 
    switch (type) {
        case 'M':
        case 'm': {
            int parsed = sscanf(cmd + 1, "%d %d %f", &joint, &steps, &speed);
            if (parsed == 3 && joint >= 1 && joint <= NUM_JOINTS) {
                stepper_move(joint - 1, steps, speed);
            } else if (parsed == 2 && joint >= 1 && joint <= NUM_JOINTS) {
                stepper_move(joint - 1, steps, DEFAULT_SPEED);
            } else {
                Serial.println("[ERR] Usage: M <joint 1-5> <steps> [speed]");
            }
            break;
        }
 
        case 'H':
        case 'h': {
            if (sscanf(cmd + 1, "%d", &joint) == 1 &&
                joint >= 1 && joint <= NUM_JOINTS) {
                stepper_home(joint - 1);
            } else {
                Serial.println("[ERR] Usage: H <joint 1-5>");
            }
            break;
        }
 
        case 'S':
        case 's': {
            if (sscanf(cmd + 1, "%d", &angle) == 1) {
                angle = constrain(angle, 0, 180);
                gripper.write(angle);
                servoAngle = angle;
                Serial.printf("[SERVO] Angle set to %d\n", angle);
            } else {
                Serial.println("[ERR] Usage: S <angle 0-180>");
            }
            break;
        }
 
        case 'C':
        case 'c': {
            if (sscanf(cmd + 1, "%d %d", &joint, &currentMA) == 2 &&
                joint >= 1 && joint <= NUM_JOINTS) {
                stepper_set_current(joint - 1, (uint16_t)currentMA);
            } else {
                Serial.println("[ERR] Usage: C <joint 1-5> <mA>");
            }
            break;
        }
 
        case 'P':
        case 'p': {
            for (int i = 0; i < NUM_JOINTS; i++) {
                Serial.printf("Joint %d: pos=%d homed=%s moving=%s\n",
                    i + 1,
                    joints[i].position,
                    joints[i].homed ? "yes" : "no",
                    joints[i].moving ? "yes" : "no");
            }
            Serial.printf("Servo: %d deg\n", servoAngle);
            break;
        }
 
        case 'E':
        case 'e':
            stepper_emergency_stop();
            break;
 
        case 'R':
        case 'r':
            stepper_enable_all();
            break;
 
        case '?':
            print_help();
            break;
 
        default:
            Serial.printf("[ERR] Unknown command: %c\n", type);
            break;
    }
}
 
void setup() {
    Serial.begin(115200);
    delay(2000);
 
    Serial.println();
    Serial.println("Stasis 6-DOF Robotic Arm v0.1");
 
    steppers_init();
 
    gripper.setPeriodHertz(50);
    gripper.attach(SERVO_PIN, SERVO_MIN_US, SERVO_MAX_US);
    gripper.write(servoAngle);
 
    wifi_init();
    ota_init();
    print_help();
 
    Serial.println("[READY]");
}
 
void loop() {
    if (wifiConnected) {
        ArduinoOTA.handle();
    }
 
    steppers_update();
 
    while (Serial.available()) {
        char c = Serial.read();
 
        if (c == '\n' || c == '\r') {
            cmdBuf[cmdIdx] = '\0';
            if (cmdIdx > 0) {
                process_command(cmdBuf);
            }
            cmdIdx = 0;
        } else if (cmdIdx < SERIAL_BUF_SIZE - 1) {
            cmdBuf[cmdIdx++] = c;
        }
    }
}
 

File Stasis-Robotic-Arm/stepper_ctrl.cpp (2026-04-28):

#include "stepper_ctrl.h"
 
static HardwareSerial TMCBus1(1);
static HardwareSerial TMCBus2(2);
 
static TMC2209Stepper drv1(&TMCBus1, R_SENSE, 0);
static TMC2209Stepper drv2(&TMCBus1, R_SENSE, 1);
static TMC2209Stepper drv3(&TMCBus1, R_SENSE, 2);
static TMC2209Stepper drv4(&TMCBus1, R_SENSE, 3);
static TMC2209Stepper drv5(&TMCBus2, R_SENSE, 0);
 
Joint joints[NUM_JOINTS];
 
static void configure_driver(TMC2209Stepper& drv, uint16_t currentMA) {
    drv.begin();
    drv.toff(4);
    drv.rms_current(currentMA);
    drv.microsteps(DEFAULT_MICROSTEPS);
    drv.en_spreadCycle(true);
    drv.pwm_autoscale(true);
    drv.TCOOLTHRS(0xFFFFF);
    drv.SGTHRS(50);
    drv.shaft(false);
}
 
static void init_joint(uint8_t idx, TMC2209Stepper* drv,
                       uint8_t step, uint8_t dir, uint8_t diag) {
    joints[idx].driver       = drv;
    joints[idx].stepPin      = step;
    joints[idx].dirPin       = dir;
    joints[idx].diagPin      = diag;
    joints[idx].position     = 0;
    joints[idx].target       = 0;
    joints[idx].speed        = DEFAULT_SPEED;
    joints[idx].accel        = DEFAULT_ACCEL;
    joints[idx].homed        = false;
    joints[idx].moving       = false;
    joints[idx].lastStepTime = 0;
    joints[idx].stepInterval = 0;
 
    pinMode(step, OUTPUT);
    pinMode(dir,  OUTPUT);
    pinMode(diag, INPUT);
    digitalWrite(step, LOW);
    digitalWrite(dir,  LOW);
}
 
void steppers_init() {
    TMCBus1.begin(TMC_BAUD, SERIAL_8N1, TMC_BUS1_RX, TMC_BUS1_TX);
    TMCBus2.begin(TMC_BAUD, SERIAL_8N1, TMC_BUS2_RX, TMC_BUS2_TX);
    delay(100);
 
    configure_driver(drv1, DEFAULT_CURRENT_MA);
    configure_driver(drv2, DEFAULT_CURRENT_MA);
    configure_driver(drv3, DEFAULT_CURRENT_MA);
    configure_driver(drv4, DEFAULT_CURRENT_MA);
    configure_driver(drv5, DEFAULT_CURRENT_MA);
 
    init_joint(0, &drv1, STEP_1, DIR_1, DIAG_1);
    init_joint(1, &drv2, STEP_2, DIR_2, DIAG_2);
    init_joint(2, &drv3, STEP_3, DIR_3, DIAG_3);
    init_joint(3, &drv4, STEP_4, DIR_4, DIAG_4);
    init_joint(4, &drv5, STEP_5, DIR_5, DIAG_5);
 
    Serial.println("[STEPPER] All 5 TMC2209 drivers initialised");
 
    for (int i = 0; i < NUM_JOINTS; i++) {
        uint8_t ver = joints[i].driver->version();
        Serial.printf("[STEPPER] Joint %d TMC2209 version: 0x%02X %s\n",
                      i + 1, ver, (ver == 0x21) ? "(OK)" : "(FAIL)");
    }
}
 
void stepper_move(uint8_t joint, int32_t steps, float speed) {
    if (joint >= NUM_JOINTS) return;
 
    Joint& j = joints[joint];
 
    if (steps < 0) {
        digitalWrite(j.dirPin, HIGH);
        steps = -steps;
    } else {
        digitalWrite(j.dirPin, LOW);
    }
 
    j.target       = j.position + ((digitalRead(j.dirPin) == HIGH) ? -steps : steps);
    j.speed        = speed;
    j.stepInterval = (uint32_t)(1000000.0f / speed);
    j.lastStepTime = micros();
    j.moving       = true;
 
    Serial.printf("[MOVE] Joint %d: %d steps at %.0f steps/s\n",
                  joint + 1, steps, speed);
}
 
void stepper_home(uint8_t joint) {
    if (joint >= NUM_JOINTS) return;
 
    Joint& j = joints[joint];
    Serial.printf("[HOME] Homing joint %d...\n", joint + 1);
 
    uint32_t homeInterval = (uint32_t)(1000000.0f / 100.0f);
    digitalWrite(j.dirPin, HIGH);
    j.driver->SGTHRS(30);
 
    bool stalled = false;
    uint32_t timeout = millis() + 30000;
 
    while (!stalled && millis() < timeout) {
        digitalWrite(j.stepPin, HIGH);
        delayMicroseconds(2);
        digitalWrite(j.stepPin, LOW);
        delayMicroseconds(homeInterval);
 
        if (digitalRead(j.diagPin) == HIGH) {
            stalled = true;
        }
    }
 
    if (stalled) {
        j.position = 0;
        j.target   = 0;
        j.homed    = true;
        Serial.printf("[HOME] Joint %d homed successfully\n", joint + 1);
    } else {
        Serial.printf("[HOME] Joint %d homing TIMEOUT\n", joint + 1);
    }
 
    j.driver->SGTHRS(50);
    j.moving = false;
}
 
void stepper_set_current(uint8_t joint, uint16_t mA) {
    if (joint >= NUM_JOINTS) return;
    joints[joint].driver->rms_current(mA);
    Serial.printf("[CURRENT] Joint %d set to %d mA\n", joint + 1, mA);
}
 
void stepper_emergency_stop() {
    for (int i = 0; i < NUM_JOINTS; i++) {
        joints[i].moving = false;
        joints[i].driver->toff(0);
    }
    Serial.println("[E-STOP] All motors disabled");
}
 
void stepper_enable_all() {
    for (int i = 0; i < NUM_JOINTS; i++) {
        joints[i].driver->toff(4);
    }
    Serial.println("[ENABLE] All motors re-enabled");
}
 
void steppers_update() {
    uint32_t now = micros();
 
    for (int i = 0; i < NUM_JOINTS; i++) {
        Joint& j = joints[i];
        if (!j.moving) continue;
 
        if (j.position == j.target) {
            j.moving = false;
            Serial.printf("[DONE] Joint %d reached position %d\n",
                          i + 1, j.position);
            continue;
        }
 
        if ((now - j.lastStepTime) >= j.stepInterval) {
            digitalWrite(j.stepPin, HIGH);
            delayMicroseconds(2);
            digitalWrite(j.stepPin, LOW);
 
            if (digitalRead(j.dirPin) == LOW) {
                j.position++;
            } else {
                j.position--;
            }
 
            j.lastStepTime = now;
 
            if (digitalRead(j.diagPin) == HIGH) {
                j.moving = false;
                Serial.printf("[STALL] Joint %d stalled at position %d\n",
                              i + 1, j.position);
            }
        }
    }
}

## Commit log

2026-04-11 Add files via upload
    Schematic
    [Stasis-Robotic-Arm.kicad_pcb, Stasis-Robotic-Arm.kicad_sch]
2026-04-29 Initialize README with project details and BOM
    Added project description, images, and bill of materials (BOM) for the robotic arm.
2026-05-17 Revise README with project overview and purpose
    Updated the overview and purpose sections, added details about the robotic arm's components and capabilities.
2026-05-17 Create 3D printer files
